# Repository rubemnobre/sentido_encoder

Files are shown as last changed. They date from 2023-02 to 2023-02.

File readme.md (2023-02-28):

sentido_encoder
============

Digital circuit to indicate the direction of spin of a quadrature pulse encoder.

###  Motivation

This circuit was developed to reduce the need for specific quadrature pulse encoder peripherals on the Controller Board of a robotics system with a large amount of encoders. It is designed to go inline with the encoder cable, read one of the pulse channels and pass it forward, and use it's relation with the other one to drive an open collector output indicating the direction of spin.

### Architecture

The usage of a small and low cost microcontroller allows for a very simple circuit, with only a LDO to supply the 5V rail, optional pull down resistors on the A and B lines to provide adaptability for different encoder output types, and a BJT with an open collector output for the direction signal.

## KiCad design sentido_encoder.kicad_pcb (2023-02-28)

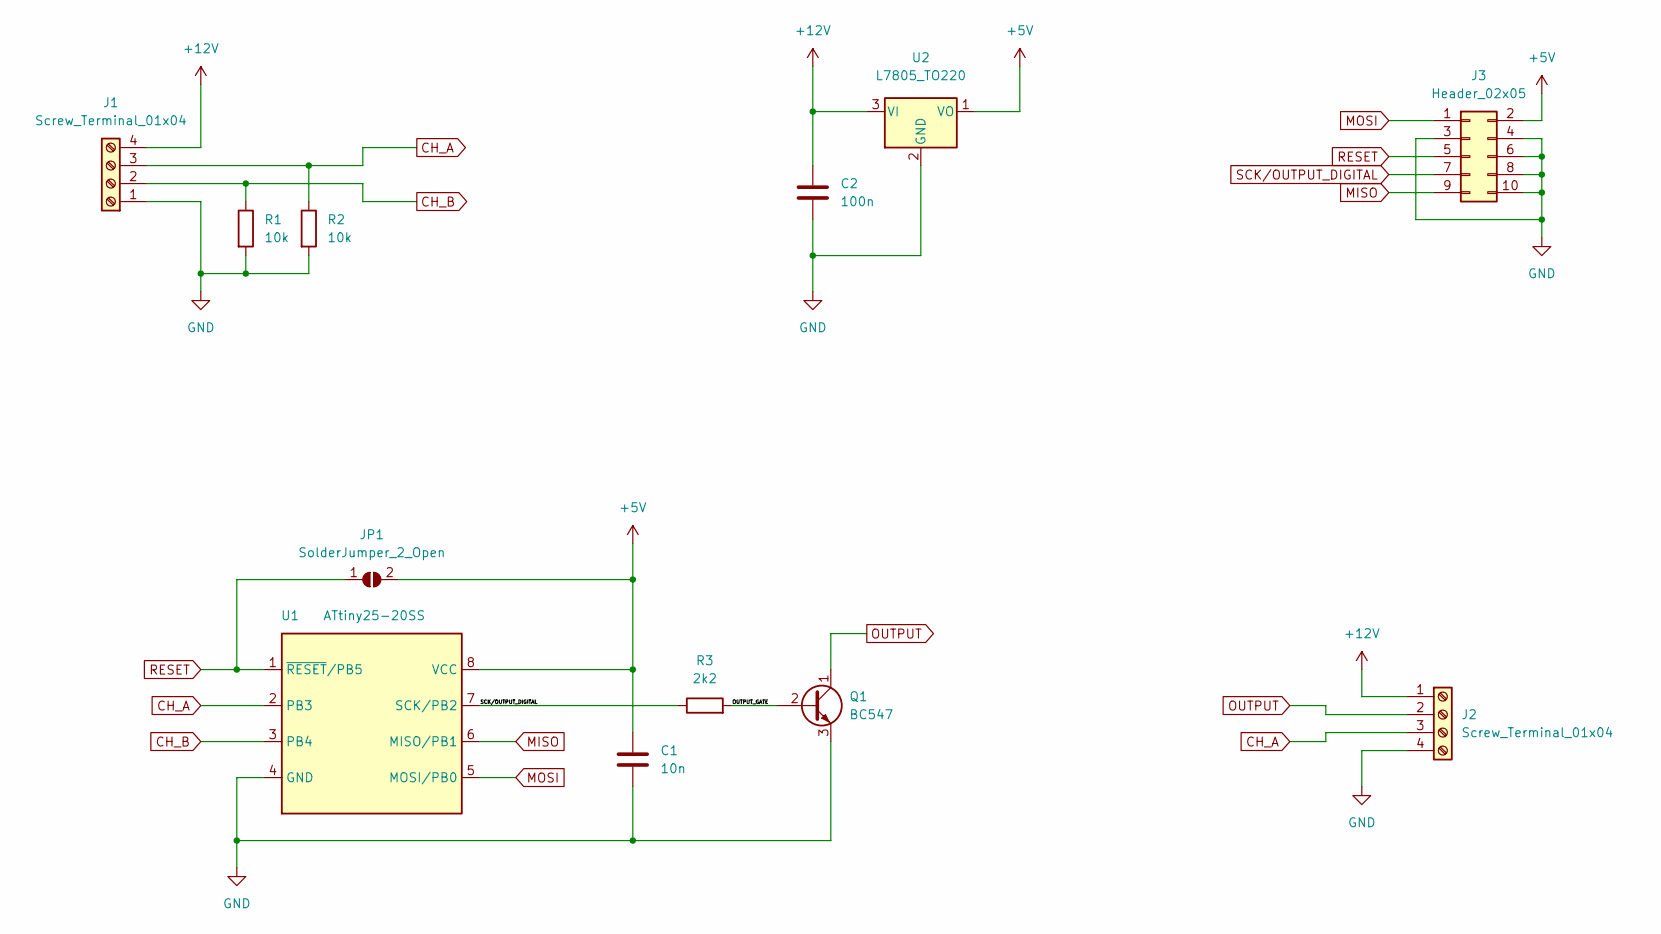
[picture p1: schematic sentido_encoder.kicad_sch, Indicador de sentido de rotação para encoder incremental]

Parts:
C1: 10n; C_Disc_D5.0mm_W2.5mm_P5.00mm
C2: 100n; C_Disc_D5.0mm_W2.5mm_P5.00mm
J1, J2: Screw_Terminal_01x04; TerminalBlock_RND_205-00234_1x04_P5.08mm_Horizontal
J3: Header_02x05; PinHeader_2x05_P2.54mm_Vertical
JP1: SolderJumper_2_Open; R_0805_2012Metric_Pad1.20x1.40mm_HandSolder
Q1: BC547; TO-92_Inline_Wide
R1, R2: 10k; R_Axial_DIN0207_L6.3mm_D2.5mm_P10.16mm_Horizontal
R3: 2k2; R_Axial_DIN0207_L6.3mm_D2.5mm_P10.16mm_Horizontal
U1: ATtiny25-20SS; SOIC-8_3.9x4.9mm_P1.27mm
U2: L7805_TO220; TO-220-3_Horizontal_TabDown

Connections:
+5V: C1.1, J3.2, JP1.2 (B), U1.8 (VCC), U2.1 (VO)
+12V: C2.1, J1.4, J2.1, U2.3 (VI)
/OUTPUT_GATE: Q1.2 (B), R3.2
CH_A: J1.3, J2.3, R2.1, U1.2 (PB3)
CH_B: J1.2, R1.1, U1.3 (PB4)
GND: C1.2, C2.2, J1.1, J2.4, J3.3, J3.4, J3.6, J3.8, J3.10, Q1.3 (E), R1.2, R2.2, U1.4 (GND), U2.2 (GND)
MISO: J3.9, U1.6 (MISO/PB1)
MOSI: J3.1, U1.5 (MOSI/PB0)
OUTPUT: J2.2, Q1.1 (C)
RESET: J3.5, JP1.1 (A), U1.1 (~RESET/PB5)
SCK/OUTPUT_DIGITAL: J3.7, R3.1, U1.7 (SCK/PB2)

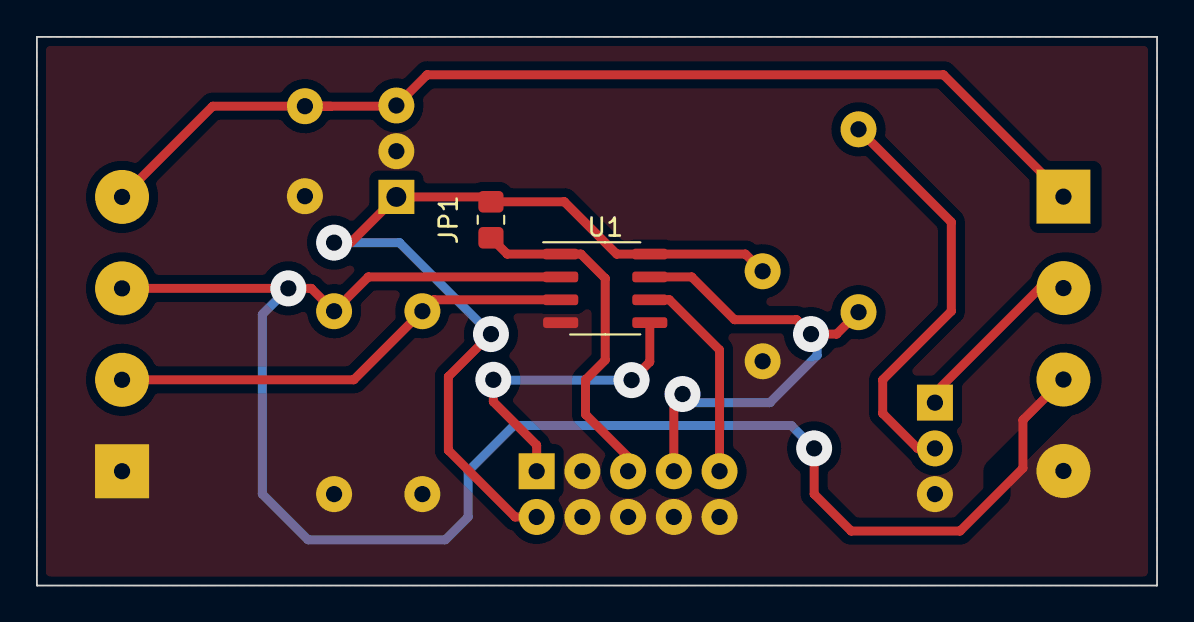
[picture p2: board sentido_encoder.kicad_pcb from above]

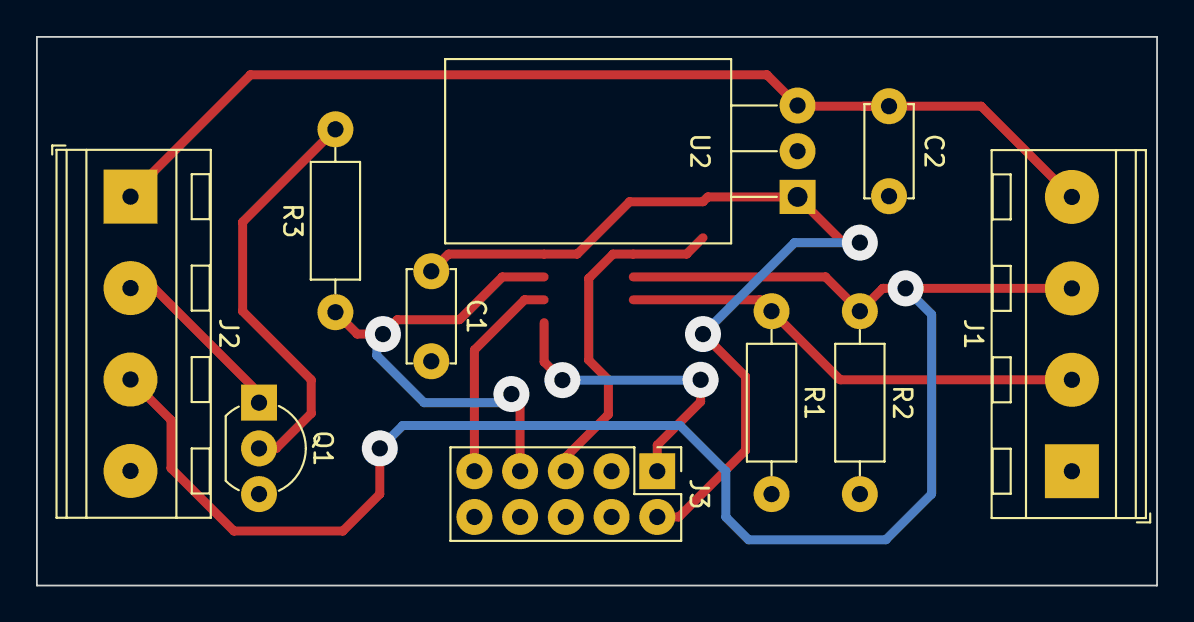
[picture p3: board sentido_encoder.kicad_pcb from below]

Board: 2 copper layers, 62.2 x 30.5 mm, 12 parts (10 on the bottom side), 11 nets.

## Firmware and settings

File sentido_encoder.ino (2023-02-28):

#include<avr/interrupt.h>
#define PB4 0b00010000
#define PB3 0b00001000
#define PB2 0b00000100
#define PCIE 0b00100000
#define PCINT3 0b00001000
#define PCINT4 0b00010000
#define GIE 0b10000000

int main() {
  GIMSK |= PCIE; // Habilita pin change interrupt
  PCMSK |= PCINT3 | PCINT4; // Habilita PCINT para os pinos 2 e 3
  
  PORTB |= PB3 | PB4; // Seta pinos 2 e 3 como high antes de configurar como input para habilitar pull up
  DDRB |= PB2; // Configura o pino 7 como output e os outros como input

  SREG |= GIE; // Habilita interrupts globalmente

  while(1);
}

volatile uint8_t ab_ant = 0, ab = 0;
int a = 0;
volatile uint8_t dir = 0, dir_ant = 0;

ISR(PCINT0_vect){ // Interrupção de pin change
  ab = PINB & (PB3 | PB4);

  // dir = 0 => 00, 01, 11, 10, 00
  // dir = 1 => 00, 10, 11, 01, 00
  uint16_t x = (ab_ant >> 1)|(ab >> 3); //A'B'AB
  switch(x){ // Lógica para definição do sentido de rotação, baseada em (ab_anterior, ab_atual)
    case 0b0001: // (00, 01) => dir = 0
      dir = 0;
      break;
    case 0b0010: // (00, 10) => dir = 1
      dir = 1;
      break;
    case 0b0100: // (00, 10) => dir = 1
      dir = 1;
      break;
    case 0b0111: // (01, 11) => dir = 0
      dir = 0;
      break;
    case 0b1000: // (10, 00) => dir = 0
      dir = 0;
      break;
    case 0b1011: // (10, 11) => dir = 1
      dir = 1;
      break;
    case 0b1101: // (11, 01) => dir = 1
      dir = 1;
      break;
    case 0b1110: // (11, 10) => dir = 0
      dir = 0;
      break;
  }

  if(dir != dir_ant){ // Contar quatro bordas na mesma direção para desconsiderar pulsos incompletos
    a = 0;
  }else{
    a++;
    if(a >= 4){
      PORTB = dir?(PORTB & ~PB2):(PORTB | PB2); // Atribui o valor da direção ao pino PB2
    }
  }

  dir_ant = dir;
  ab_ant = ab;
}
